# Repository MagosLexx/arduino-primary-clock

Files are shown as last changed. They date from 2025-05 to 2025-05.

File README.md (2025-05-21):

# Проект точного управления электромеханическими часами через Arduino с автоматической сменой полярности импульсов.

- Arduino Clock Driver with DS3231 RTC
- Первичные часы на Ардуино с DS3231 RTC
- ⏰ Arduino Clock Driver | DS3231 + L298N | 🔄 Polarity switching | 💡 D4 LED | 📜 MIT License
- ⏰ Первичные часы на Ардуино | DS3231 + L298N | 🔄 Смена полярности | 💡 D4 Светодиод | 📜 Лицензия MIT





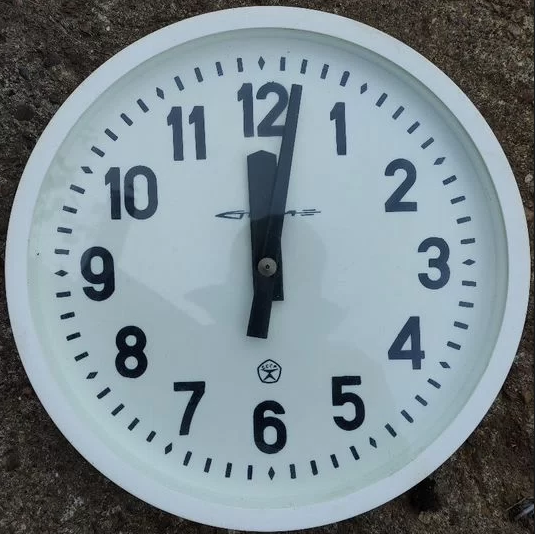
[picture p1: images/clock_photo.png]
[](./images/clock_photo.png)

## 📋 Содержание
- [Особенности](#-особенности)
- [Общее описание](#-общее-описание)
- [Аппаратные компоненты](#-аппаратные-компоненты)
- [Документация](#-документация)
- [Ввод в работу](#-ввод-в-работу)
- [Заключение](#-заключение)

## 🌟 Особенности
- ⏱ Высокоточный хронометраж (±2ppm) RTC DS3231
- 🔄 Автоматическая смена полярности каждую минуту
- ⚡ Поддержка силовых драйверов L298N (12V/24V)
- 💡 Визуальная индикация состояния (D4)
- 📅 Длительная работа без обслуживания

## 📝 Общее описание
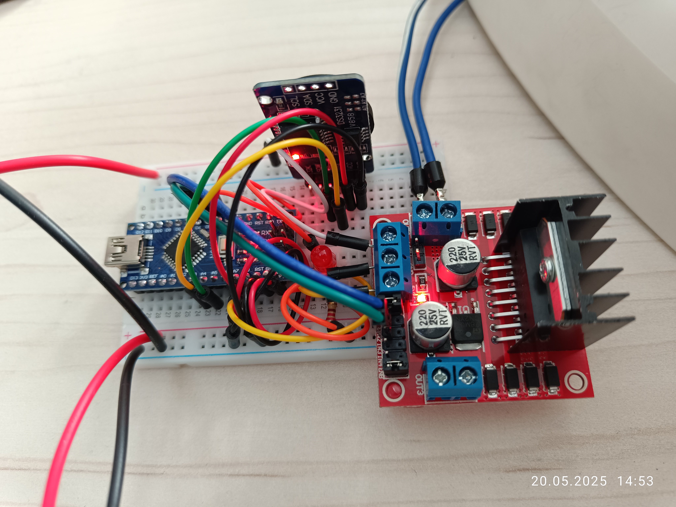
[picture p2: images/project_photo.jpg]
[](./images/project_photo.jpg)
- Данный проект разработан для ввода в строй вторичных часов "Стрела".
- Вторичные часы "Стрела", как и любые другие вторичные часы советского производства, не имеют в своём составе задаюшего тактового генератора (первичные часы), который обеспечивает выдачу импульсов на механизм передвижения стрелок. В составе вторичных часов имеется только соленоид электромагнитного привода стрелок и передаточный шестерёнчатый механизм.
- Особенностью работы механизма привода стрелок вторичных часов "Стрела" является то, что импульсы, поступающие на соленоид привода, должны менять свою полярность при каждой подаче напряжения, что реализовано в коде.
- В данном проекте не используется аккумулятор в RTC-модуле, т.к. на часах имеются только часовая и минутная стрелки и хранить дату и время в модуле не нужно. По сути, модуль DS3231 используется как высокоточный счётчик секунд с термокомпенсацией. Проверка корректности показаний модуля и сброс в случае необходимости  реализованы в коде. Использование в проекте RTC-модулей без термокомпенсации не рекомендуется. 
- Краткое описание работы устройства:
  - После загрузки проверяется состояние RTC-модуля, в случае определения некорректных данных даты и времени происходит автоматический сброс на 2000:1:1:00:00:00. В случае неисправности модуля или отсутствия связи с ним, светодиод, подключенный к пину D4 Arduino, мигает с частотой два раза в секунду в бесконечном цикле до перезагрузки системы. При пропадании связи с RTC-модулем в процессе работы часы останавливаются, однозначно сигнализируя о неисправности. 
  - Программа два раза в секунду проверяет состояние "секунд", выдаваемых RTC-модулем, когда это состояние становится равным "00", на исполнительный механизм часов через силовой блок L298N выдаётся импульс напряжения 24 В (о чём свидетельствует кратковременное включение светодиода подключенного к пину D4 Arduino), длительностью одну секунду. Длительность подаваемого импульса подбирается таким образом, чтобы обеспечить чёткое срабатывание механизма часов и может быть изменена программно. Выставлять длительность подаваемого импульса более одной секунды не рекомендуется, во избежание ненужного нагрева силовых и индуктивных элементов системы.  

## 🛠 Аппаратные компоненты
| Компонент | Количество | Примечание |
|---|---|--- |
| Arduino Nano | 1 | Любая совместимая версия |
| Модуль DS3231 | 1 | С аккумулятором LIR2032. (Необязательно)  |
| Драйвер L298N | 1 | С радиатором |
| Блок питания 12V | 1 | Для логической части |
| Блок питания 24V | 1 | Для часового механизма |
| Светодиод | 1 | Индикация срабатывания |
| Резистор 220 Ом | 1 | Для светодиода |

## ✅ Документация
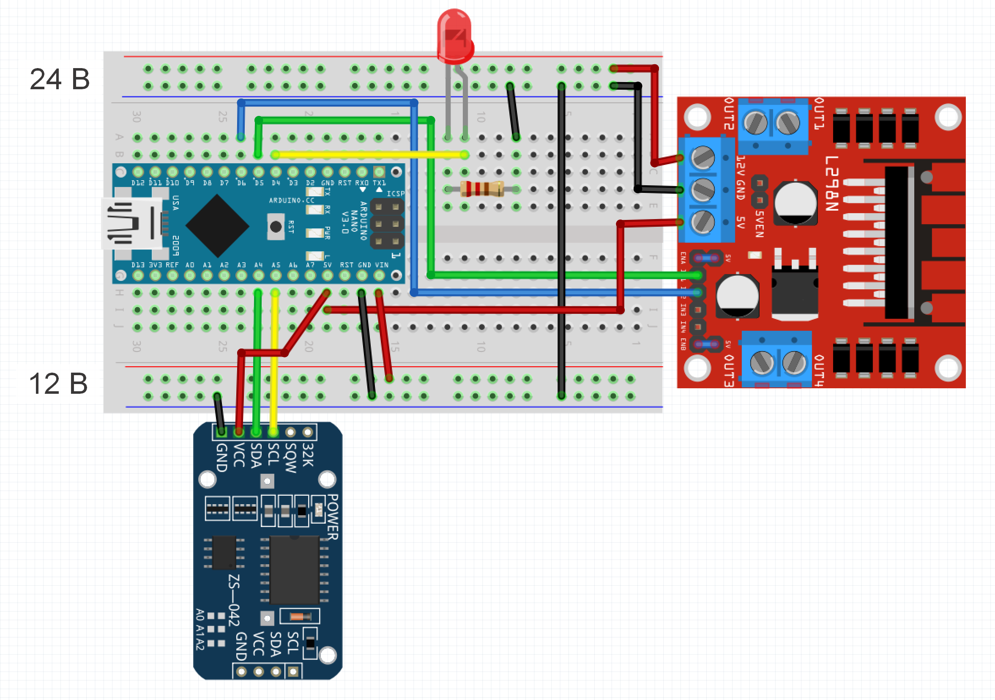
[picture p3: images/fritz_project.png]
[](./images/fritz_project.png)
- Прототипированная плата с компонентами (скриншот из Fritzing).
- При монтаже особое внимание следует уделить перемычкам на модуле L298N.
  - Перемычки 5V -- ENA и 5V -- ENB должны быть установлены.
  - Перемычка 5V -- EN должна быть снята.
- [Проект Fritzing (.fzz)](./documents/fritz_project.fzz)
- [Скетч (.ino)](./sketch/sketch.ino)
- [Скетч (.txt)](./sketch/sketch.txt)
- [Проект на одном листе (.pdf)](./documents/one_page.pdf)
- [Проект на одном листе (.vsdx)](./documents/one_page.vsdx)
- [Паспорт часов (.pdf)](./documents/passport_strela.pdf)
- [Техническая спецификация DS3231 (.pdf)](./documents/ds3231.pdf)
- [Техническая спецификация L298N (.pdf)](./documents/l298.pdf)

## 🚨 Ввод в работу
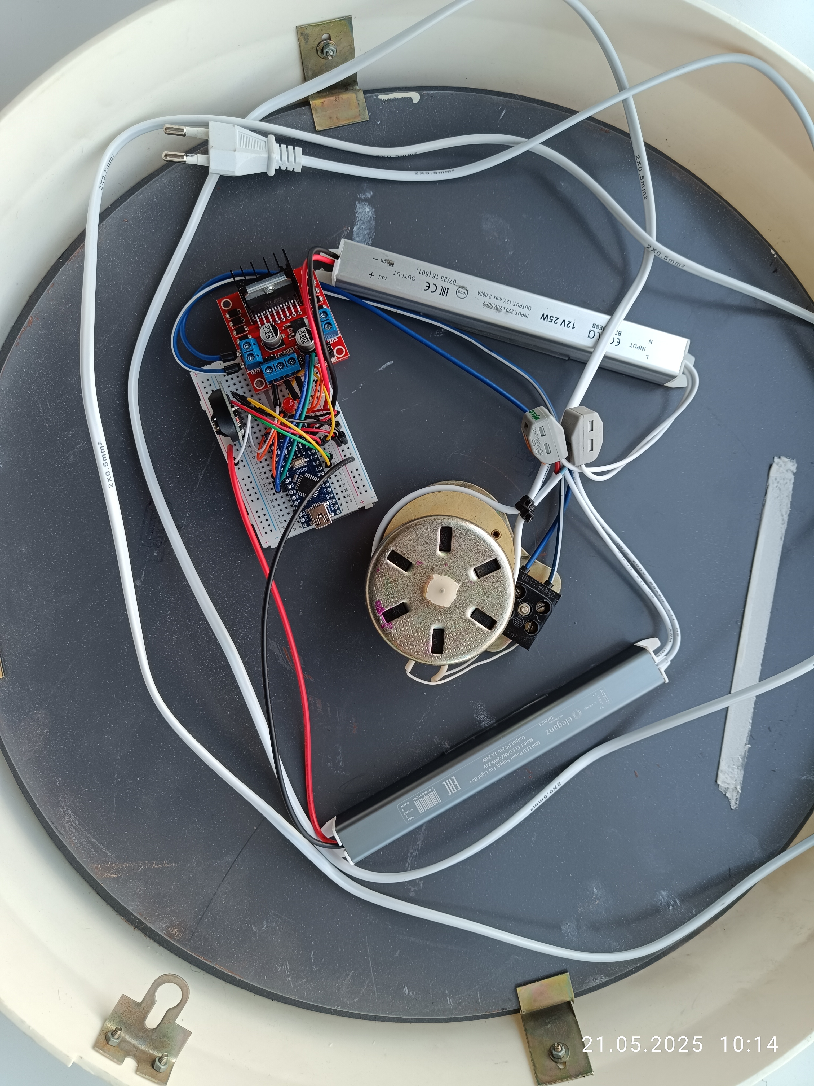
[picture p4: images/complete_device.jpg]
[](./images/complete_device.jpg)
- После подачи питания, либо перезагрузки с кнопки на Arduino, устройство выдаёт первый импульс примерно через две секунды. Не факт, что этот импульс приведёт к срабатыванию стрелочного механизма часов, т.к. в этот момент соленоид привода может уже находиться в сработанном положении для данной полярности импульса. Поэтому сначала нужно выяснить на каком положении минутной стрелки происходит старт. Варианта всего два - это чётные или нечётные минуты.
- Порядок запуска:
  - Определить с каких минут, чётных или нечётных, происходит запуск часов с первого импульса, поочередно выставляя минутную стрелку на чётные и нечётные минуты и перезагружая Arduino.
  - Допустим, старт происходит с чётных минут и время выставлено на 12:30 (при обесточенной схеме), далее, нужно дождаться контрольного времени 12:30:58 и подать на схему питание.
  - Всё, ввод в работу осуществлён.

## 🎯 Заключение
- Следует понимать что успех реализации проекта зависит в том числе и от состояния механизма самих часов. Если механизм находится в неудовлетворительном состоянии (грязь, ржавчина), то возможны пропуски хода, нечёткое срабатывание и прочие неполадки. 
- Устройство не требует обслуживания, интернет для работы также не требуется.
- Потребляемый соленоидом привода ток составляет 22-24мА, что вполне позволяет увеличить автономность системы, используя источники энергии не связанные с электрической сетью. При этом будет целесообразно минимизировать длительность управляющего импульса до минимальной величины, достаточной для чёткого срабатывания механизма часов.

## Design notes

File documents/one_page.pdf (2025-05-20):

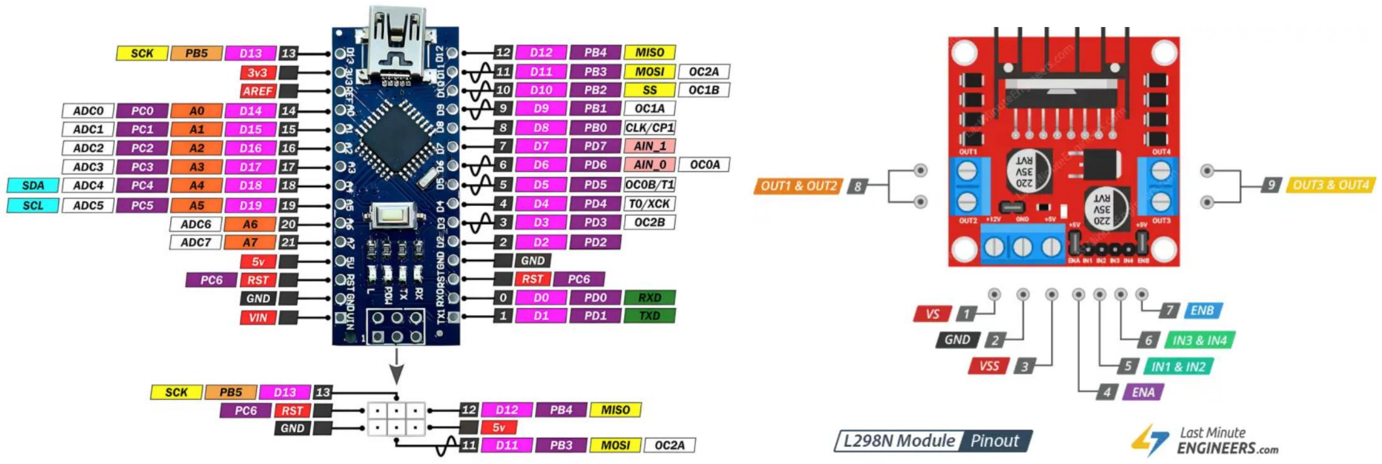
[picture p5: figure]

Данный проект позволяет вернуть в строй вторичные часы «СТРЕЛА».

В данном проекте Arduino Nano, управляя модулем L298N, подаёт на исполнительный механизм часов импульсы каждую минуту, каждый раз меняя полярность подаваемого напряжения, что связано с особенностями механизма часов.
Питание Arduino Nano

– 12
В
Питание цепей логики L298N

– 5
В

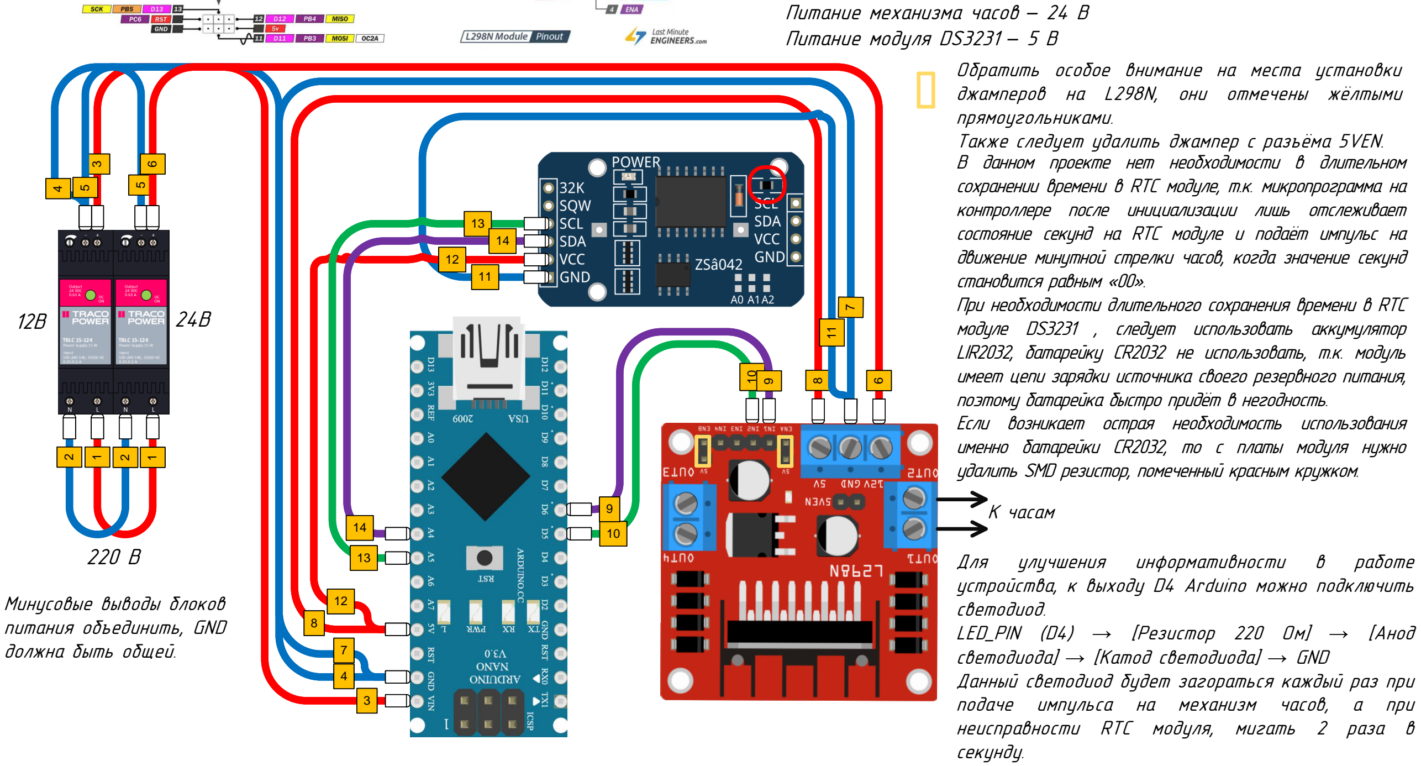
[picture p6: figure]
Питание механизма часов; Питание модуля DS3231; прямоугольниками.; контроллере после инициализации лишь отслеживает; становится равным «00».; Если возникает острая необходимость использования; Минусовые выводы блоков питания объединить, GND должна быть общей.; К часам; Для; улучшения; информативности; работе; светодиод. LED_PIN (D4); → [Резистор 220 Ом]; → [Анод; светодиода]; → [Катод светодиода]; → GND; секунду.

Обратить особое внимание на места установки джамперов на L298N, они отмечены жёлтыми

Также следует удалить джампер с разъёма 5VEN. В данном проекте нет необходимости в длительном сохранении времени в RTC модуле, т.к. микропрограмма на

состояние секунд на RTC модуле и подаёт импульс на движение минутной стрелки часов, когда значение секунд

При необходимости длительного сохранения времени в RTC модуле DS3231 , следует использовать аккумулятор LIR2032, батарейку CR2032 не использовать, т.к. модуль имеет цепи зарядки источника своего резервного питания, поэтому батарейка быстро придёт в негодность.

именно батарейки CR2032, то с платы модуля нужно удалить SMD резистор, помеченный красным кружком.

устройства, к выходу D4 Arduino можно подключить

Данный светодиод будет загораться каждый раз при подаче импульса на механизм часов, а при неисправности RTC модуля, мигать 2 раза в

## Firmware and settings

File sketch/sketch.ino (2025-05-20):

/*
 * Скетч для управления часовым механизмом через RTC DS3231
 * Лицензия: MIT
 * Автор: MagosLexx, 2025
 * GitHub: https://github.com/MagosLexx/arduino-primary-clock
 */

// 1. Подключение необходимых библиотек
#include <Wire.h>      // Для работы с I2C-интерфейсом
#include <RTClib.h>    // Для работы с модулем реального времени

// 2. Конфигурация аппаратных пинов (тип uint8_t - оптимальный для номеров пинов)
const uint8_t IN1 = 5;      // Пин управления первой катушкой (MOSFET/драйвер)
const uint8_t IN2 = 6;      // Пин управления второй катушкой (MOSFET/драйвер)
const uint8_t LED_PIN = 4;  // Пин для светодиодной индикации (D4)

// 3. Параметры временных интервалов (тип unsigned long для точного учёта времени)
const unsigned long PULSE_DURATION = 1000UL;    // Длительность импульса в миллисекундах
const unsigned long DEBOUNCE_DELAY = 100UL;    // Защитный интервал после импульса
const unsigned long TIME_CHECK_INTERVAL = 500UL;// Проверка времени каждые 500 мс
const unsigned long LED_DURATION = 1000UL;     // Длительность свечения светодиода (1 сек)

// 4. Глобальные переменные состояния
RTC_DS3231 rtc;           // Объект для работы с RTC-модулем
bool pulsePolarity = true; // Флаг текущей полярности импульса
uint8_t lastMinute = 255;  // Хранит последнюю обработанную минуту (255 - начальное невалидное значение)
unsigned long lastTimeCheck = 0; // Время последней проверки
unsigned long ledStartTime = 0;  // Время включения светодиода
bool ledActive = false;          // Флаг активности светодиода

void setup() {
  // 5. Инициализация цифровых выходов
  pinMode(IN1, OUTPUT);    // Настройка IN1 как выхода
  pinMode(IN2, OUTPUT);    // Настройка IN2 как выхода
  pinMode(LED_PIN, OUTPUT);// Настройка светодиода как выхода
  digitalWrite(IN1, LOW);  // Гарантированное выключение при старте
  digitalWrite(IN2, LOW);  // Гарантированное выключение при старте
  digitalWrite(LED_PIN, LOW); // Выключение светодиода

  // 6. Инициализация I2C-шины с дополнительными параметрами
  Wire.begin();            // Старт I2C-интерфейса
  Wire.setTimeout(100);    // Установка таймаута 100 мс для операций

  // 7. Инициализация модуля реального времени
  if (!rtc.begin()) {      // Проверка подключения DS3231
    // Критическая ошибка - модуль не обнаружен
    while (true) {         // Бесконечный цикл
      // Аварийная индикация светодиодом
      digitalWrite(LED_PIN, HIGH);
      delay(200);
      digitalWrite(LED_PIN, LOW);
      delay(200);
    }
  }

  // 8. Коррекция времени при необходимости
  if (rtc.lostPower() || rtc.now().year() < 2020) {
    rtc.adjust(DateTime(2000, 1, 1, 0, 0, 0)); // Установка "эталонного" времени
  }
}

void loop() {
  // 9. Управление светодиодом (выключение по истечении времени)
  if (ledActive && (millis() - ledStartTime >= LED_DURATION)) {
    digitalWrite(LED_PIN, LOW);
    ledActive = false;
  }

  // 10. Проверяем время только если прошло более 500 мс с последней проверки
  if (millis() - lastTimeCheck >= TIME_CHECK_INTERVAL) {
    lastTimeCheck = millis();
    
    // 11. Получение текущего времени от RTC
    DateTime now = rtc.now(); // Чтение временной метки
    
    // 12. Условие срабатывания (с двойной проверкой):
    // - Текущая минута ≠ последней обработанной
    // - Секунды = 0 (начало минуты)
    if (now.minute() != lastMinute && now.second() == 0) {
      lastMinute = now.minute(); // Фиксация обработанной минуты
      
      // 13. Активация светодиода
      digitalWrite(LED_PIN, HIGH);
      ledStartTime = millis();
      ledActive = true;
      
      // 14. Подача управляющего импульса
      digitalWrite(IN1, pulsePolarity ? HIGH : LOW);
      digitalWrite(IN2, pulsePolarity ? LOW : HIGH);
      delay(PULSE_DURATION);
      
      // 15. Гарантированное выключение катушек
      digitalWrite(IN1, LOW);
      digitalWrite(IN2, LOW);
      
      // 16. Смена полярности с защитой от прерываний
      noInterrupts();
      pulsePolarity = !pulsePolarity;
      interrupts();
      
      // 17. Точная выдержка защитного интервала
      unsigned long start = millis();
      while (millis() - start < DEBOUNCE_DELAY) {}
    }
  }
  
  // 18. Фоновая пауза для снижения нагрузки
  delay(10);
}

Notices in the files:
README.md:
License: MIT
